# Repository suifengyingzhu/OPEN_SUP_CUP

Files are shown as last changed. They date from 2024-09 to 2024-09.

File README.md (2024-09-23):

# RM2024桂电数控超级电容方案开源

设计者：杨宇翔

文档撰写：杨宇翔 钟启源 刘宇轩

桂林电子科技大学Evolution战队

## 前言

在RoboMaster机甲大师赛事中，严苛的底盘功率限制规则迫使各参赛队伍从软件和硬件方面研究高效的功率管理方案。而我队早在2018年末便研究并开源了较具有特色的超级电容方案，但2020年，官方裁判系统超级电容管理模块与相关限制规则加入，超级电容的使用更加规范，这也给我们带来了不小的挑战。



在这个赛季，我们结合本校学长的超级电容方案，经过近一赛季的研究与测试，开发出了采用4MOS结构的两相交错Buck-Boost电路构建的超级电容方案，希望能为超电的开发研究提供一个新的思路。

## 简介

本方案中的两相交错Buck-Boost变换器是一种采用载波移相180°的控制方式的电路结构。该变换器在Buck模式和Boost模式之间切换时，能够实现能量的双向流动，并且不会产生过压与过流现象。同时，交错并联的拓扑结构可以减少电感电流的纹波，降低每相电感的体积，并提高电路的响应速度，使其极其适用于超级电容的控制中。双向BuckBoost应用已经非常普遍，对于双向BuckBoost的原理在此不再赘述。

## 拓扑介绍

### 两相交错场景

#### 优劣分析

1.低纹波。上面提及，每一相电路其实是以100Khz的频率工作的，但相比于单相输出，两相交错180度可以将电流纹波进行互补输出，理论上总输出端纹波相互抵消，电压输出波形更加平稳。由于纹波消除作用，它的有效输入与输出纹波变为 200KHz。因此在计算交错式设计的电感时，适用的频率虽和单相设计完全相同，但能允许的纹波电流却会增加一倍，使得设计所需的电感值得以减少一半，电容设计也是如此，等效后电压纹波的明显降低，使得设计所需的输出电容数量减少，节约成本的同时，也大大缩小了整个模块的体积，整个电源环路设计更加简洁。

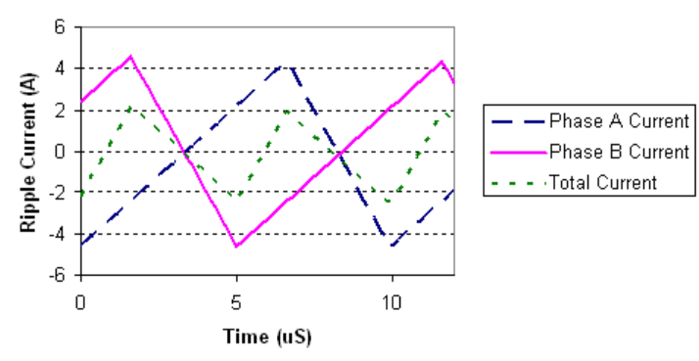
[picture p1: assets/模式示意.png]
屏幕截图 2024-07-03 203623


2.高效率。两相交错升降压电源虽然是每相将两个周期合并降频至100Khz工作，但实际总输出特性仍可等效为200Khz的工作场景。与单相相比，我们将开关管的开关频率降低，减小了开关管的开关损耗，从而进一步降低了整个电源的静态功耗，提升了整个模块的功率密度。而在负载场景下，由于每相分走一半电流，两相更好控制了电感的温度升幅，提升了模块的效率，值得一提的是，在两相交错下，电路的响应基本等同于单路电路的响应，没有受到频率降低的影响。

#### 控制方法

在低功率场景时，本方案采用两相Buck-Boost的控制方法。假设我们此时处于50%占空比时的Buck模式：在第一个周期中，第一路左边半桥的两个开关管Q1,Q2正常进行50%占空比的PWM开关，右边半桥上管Q3处于常通状态；第二路左右半桥两上管Q5,Q7处于关闭状态，两下管处于常通状态。在第二个周期中，将两路电源的开关管状态进行交换。（如图所示）

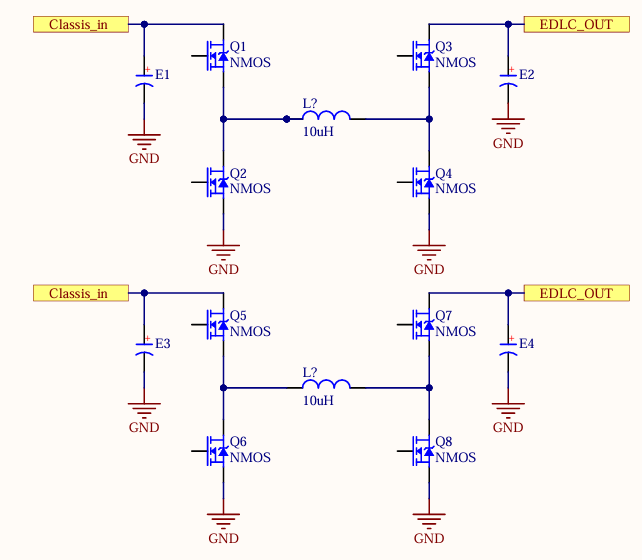
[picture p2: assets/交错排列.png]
交错排列


不难看出，两路电源每隔一个周期工作一次，并且是处于交错工作的状态。如果我们将开关频率调整至200Khz,那么此时可以把每一路电源等效为在以100Khz的频率进行开关，两相交错180度。由于我们的方案是并联两相输出，因此总输出端是互补输出的，实际整个电路的开关频率还是处于200Khz的状态。

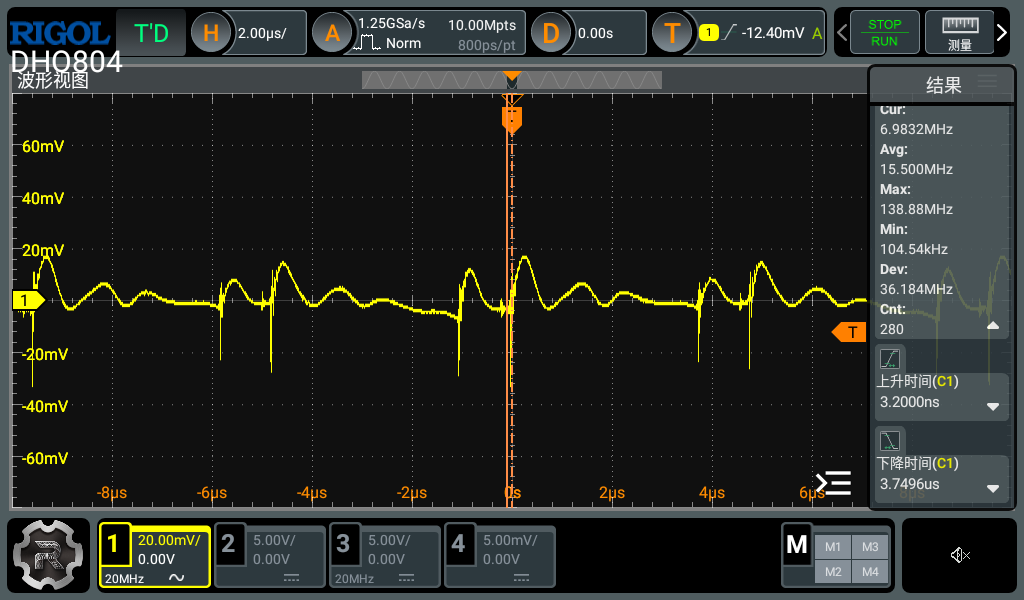
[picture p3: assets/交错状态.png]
交错状态


本超电方案的最大的劣势在于控制板上并没有太多的电容供储能使用，但电容组的存在令这一劣势的影响微乎其微，多出的空间反而使整块板的布局变得更加合理美观，功能也更加齐全，为其的使用锦上添花。

### 并联输出场景

#### 电压源并联可行性分析

 一般情况下，由于受控电压源的电压随着控制量的变化而变化，其产生的电压值不是固定不变的，根据电路理论，两个理想受控电压源中电压高的会给电压低的充电，使其电流过高，造成损坏，因此无法直接并联。

但是在实际情况下，电压源内阻以及导线电阻并非小到不能忽略。当两不同电压源同时为一个用电器供电时，根据基尔霍夫电流原理，流入等于流出，并带入数值加以计算，可以得出两电压源电压值为正数，只要保证两电压源的输出电流大于0即可保证两电压源都在向用电器输入能量。因此在实际应用中，受控电压源的并联都是采用电压源加理想二极管构成不间断电源方案，进而实现并联。然而对于双向电源来说，二极管限制了电流方向，此方案不可行。本超电方案中通过在交错状态下分时导通和并联状态下恒比例输出实现均流控制，减少环路损耗。

#### 优劣分析
对于导通损耗，损耗功率和电流的平方成正比，并联两相可以减少MOS管流过的峰值电流，减少损耗，提高效率。同时在并联状态下，电感量减半，同时带来两倍的电流斜率，此时响应也优于交错。实际控制中，采用低功率下交错，高功率和负载迁越时并联的方式，在保证最优性能的情况下最大限度降低损耗。

#### 控制方法

在高功率和负载迁越场景时，两路同步并联输出，本方案采用并联Buck-Boost的控制方法。两个并联的电压源使用。在使用时，若将右上管常导通，右下管常断开，而左上和左下管继续使用Buck电路控制策略，则完全等效于Buck电路的拓扑，此时可将电路看作同步Buck，可实现将左侧电降压后提供给右侧；若将左上常导通，左下常断开，而右上和右下继续使用Boost电路控制策略，则完全等效于Boost电路的拓扑，此时将电路看作同步Boost即可实现将左侧电升压后提供给右侧；若左右电压相近，则in半管的占空比会减少，out半管的占空比会增加，两者逐渐趋同，此时实际应用中由于最大占空比以及死区时间等限制，很难独立的使用Buck或者Boost拓扑。于是考虑用Buck控制策略控制左半桥，用Boost控制策略控制右半桥，此即为buck-boost电路。在任意时刻，电路可视为Buck电路或Boost电路。此时，无论是使用叠加原理还是通过伏秒平衡定律，我们都可以得到如下结果 Vleft/Vright=Dright/Dleft ，其中， Dleft 为左侧上管占空比， Dright 为右侧上管占空比。

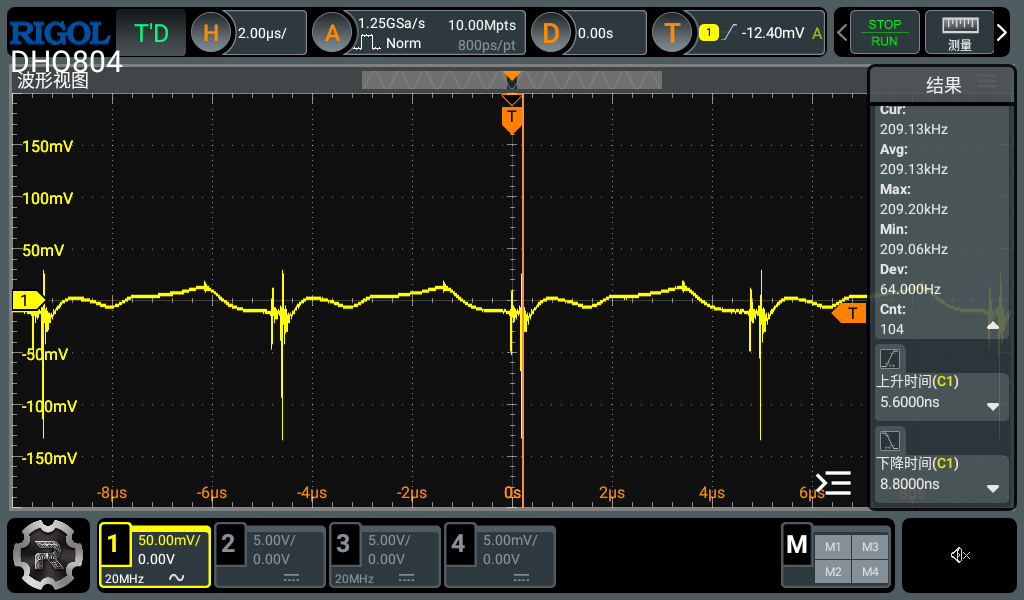
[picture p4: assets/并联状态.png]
并联状态


## 效率提升

在高负载下，超电控制模块的温度会会显著提升。一般的应对方法是利用一些降温手段，如采用铝基板、添加散热片、甚至是加装散热风扇来保证持续高负载下模块的性能。而我们更倾向于从源头解决问题——提高模块的效率，即通过一些硬件设计和软件控制的方式，降低电能转化成的热能，从而减少电能的流失，最终达成提高效率的目的。这从一方面来看，能高效地将底盘电能搬运储存，或是将超电中储存的电能最大程度输送回底盘供电，提升机器人的性能；另一方面，减少模块的发热，也就能控制模块的故障发生率，保证机器人在运行中用电的稳定性和安全性。

那么，如何提高模块的效率？首先我们要考虑的是实际使用过程中哪里会让其产生损耗，这样才能对症下药。例如，电流在回路传输过程中，导线和采样电阻都会发热；四开关管频繁的开关过程中也会产生不小的损耗；电感、电容参数计算不准确会产生更多的损耗······

接着，我们就要考虑如何尽最大可能地减少这些损耗。从分析模块的电流环路，优化PCB布局，减小电流环流面积等方面下手是个不错的选择，当然，器件的摆放也很关键，良好的布局才能保证超电拥有优异性能的同时又能有良好的散热性。下图为持续负载30A 1小时下的温度图像，分散的两个环路使得散热效率大幅提升，同时优化的电流环路在最小环路面积下使得电路损耗降低。

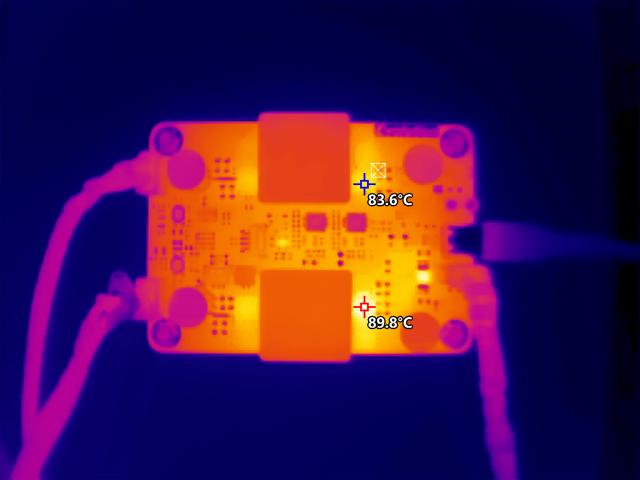
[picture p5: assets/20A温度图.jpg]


效率提升最重要在于考虑元器件所造成的损耗。在实际使用过程中，电感和开关管的发热是比较明显的，故从这二者下手。改善电感效率的重心在于参数的计算和电感的选型，我们采用的是饱和电流30A的一体成型电感，在实际测试中，两路共30A时电感温度稳定在60摄氏度左右。MOS管的损耗主要为开关损耗和导通损耗：导通损耗是MOS管在工作状态时Rds(on)产生的，公式为

P=Io²×Rds(on)

而开关损耗的产生则是因为MOS管虽然是电源型器件，但是由于极间结电容的存在，MOS管漏源极导通需要栅极驱动电流充电后才能正常打开，关闭时亦是如此，公式为

P=Qg×Vg×fsw×2

开关管所产生的损耗可以通过硬件选型和软件控制这两种方式来降低。首先是MOS管的选型，从公式不难看出产生的损耗主要是由Rds(on)和Qg这两个参数决定的，在选型时应仔细斟酌其内部材料的使用，比较得出性能更加突出的选型。当然，由于栅极上升沿时间的存在，MOS管若不能及时打开或关闭，也会造成更多的损耗，且如果续流管没有及时打开，只能通过自身的体二极管续流，此时产生的损耗是极其严重的。解决该问题的办法一般是更换Qg更小的MOS管或者增加驱动电流，我们选用的栅极驱动是LM5109，该芯片能提供持续1A的驱动电流，实测使用此芯片模块上MOS管栅极上升沿约为50纳秒，同比其他芯片更为迅速。同时，我们采用自举的方式为半桥供电，因此由于自举电容充电时间和栅极驱动时间的限制，模块不能到达100%占空比。软件降低损耗主要采用上面介绍的交错两相控制的方法，这样不仅能让两路均流，使得单路导通损耗减少，MOS管发热减小，而且将200Khz的开关频率降低一半，也能使开关损耗降低，并且将模块输出的最高占空比提高至100%。

## 多拓扑结构 

模块预留了两个大电流跳线点，通过改变跳线点的连接状态，可将结构改为双通道独立输入输出，单通道交流输出，升降压稳压型UPS（输出稳压型超电，如30v供电轮系）如下图所示，为备赛电赛提供更多选择。对于这些拓扑结构都已进行验证，这部分的代码之后将示完成度开源。
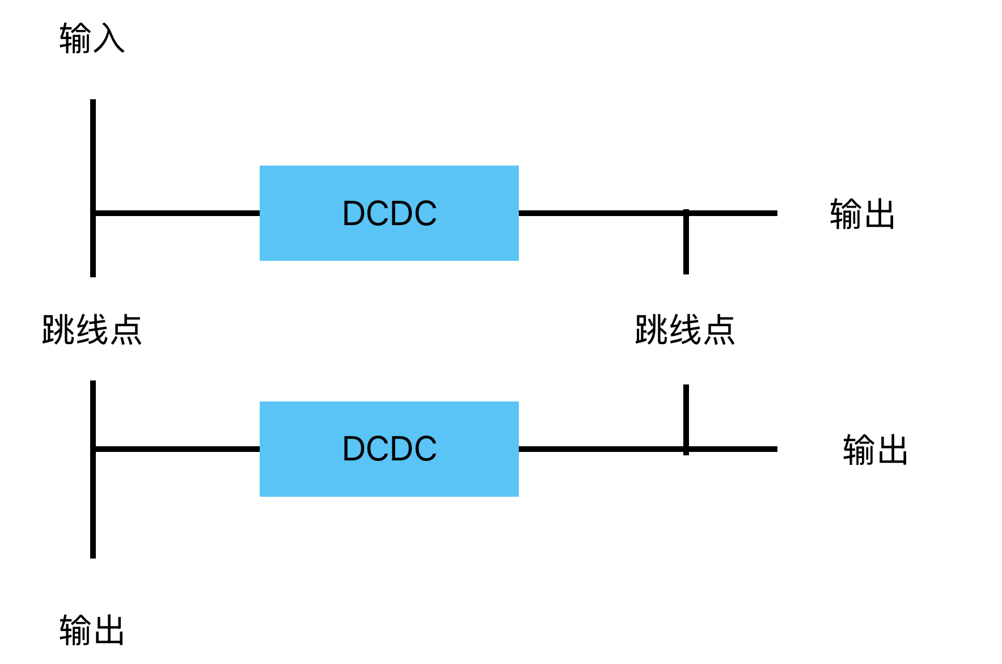
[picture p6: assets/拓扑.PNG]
拓扑


## 输入输出参数

### 额定最大值

输入电压8-30V，电容端单通道瞬态30A，持续负载10A。双通道瞬态60A（电容组60A恒流输出持续到没电），持续负载20A.（无散热片和风冷）

电容端输出2-30V，底盘输出端12-30V（单通道升压版可到40V）

### 输出波纹值

可以对输入，输出，电容组处电压进行测量，监测控制模块的实际输出电压。

确保输出电压在设定范围800mV内，静态波纹70mv, 10W-400W迁越负载电压波动1200mV，1A-20A ,2500mA/us负载斜率下恢复时间1ms。具备多端电流测量，监测功率控制模块的实际输出电流。确认输出电流与设定值相符，辅助功率控制，并在需要时进行调整。

## 保护机制

超电烧毁乃兵家常事，为保证超电正常稳定运行，项目成立之初就提出要完善其自身的保护机制，延长其使用寿命。（超电控制板成本在200元左右，也是为了减少此项支出）

硬件件具备输入输出TVS、输入欠压保护机制。

软件具备过载、电容组过压、输入欠压、电容组欠压、模组元器件损坏的保护机制，并可在模块无永久性损坏风险的情况下自行恢复。

确认保护触发后，系统能够在1ms内停机或采取其他适当的措施。

触发自锁保护后，仅能在模块状态正常后通过断电重启解除保护，系统严重损坏后保护可能失效。

自锁保护状态：输入欠压保护，电容端过压保护，输出端过压保护（刹车时产生过高电动势，超级电容无法完全吸收），过流保护，MOS损坏保护

得益于交错模式的超快响应和极强的过流能力，虽然设有如上保护，但其从未在赛场上触发，从联盟赛上场至今，超电在赛场上保持着0失误的记录。

## 上位机

为方便功能的维护和升级，还配套制作了上位机程序。由于控制逻辑过于复杂，为保证逐周期环路计算，代码不得不做许多优化，包括但不限于大量内敛，导致代码逻辑十分混乱，且没有注释，代码部分待优化完成后开源，如需尝鲜的兄弟可以通过上位机下载代码。

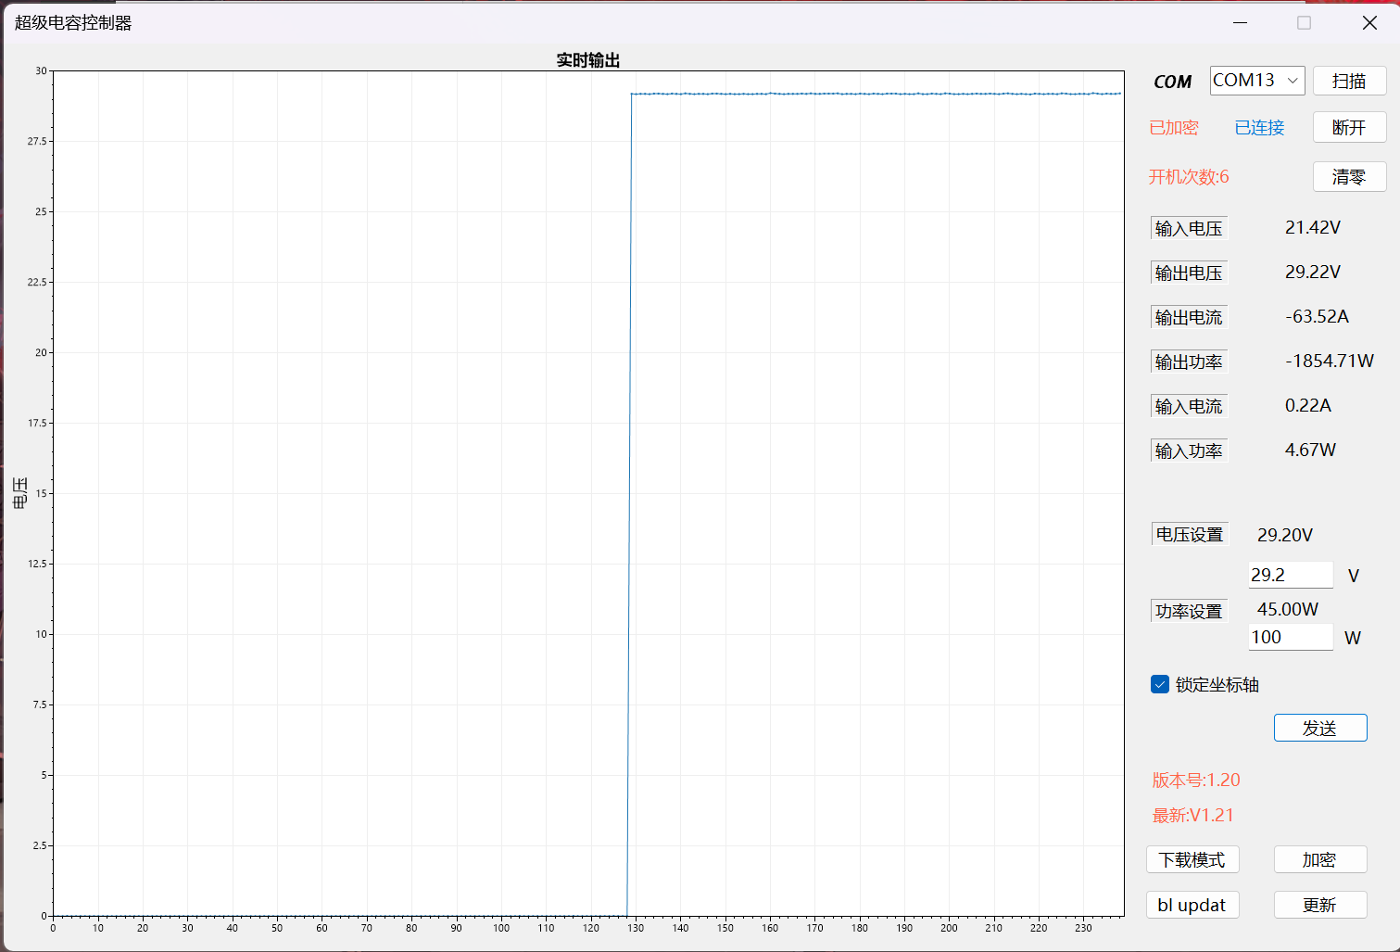
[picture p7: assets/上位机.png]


因代码中没有使用输出电流检测，故大部分板子没有焊电流感应放大器，该功能正常可用。

## 结语

祝愿大家超电永远不烧！！！

联系方式
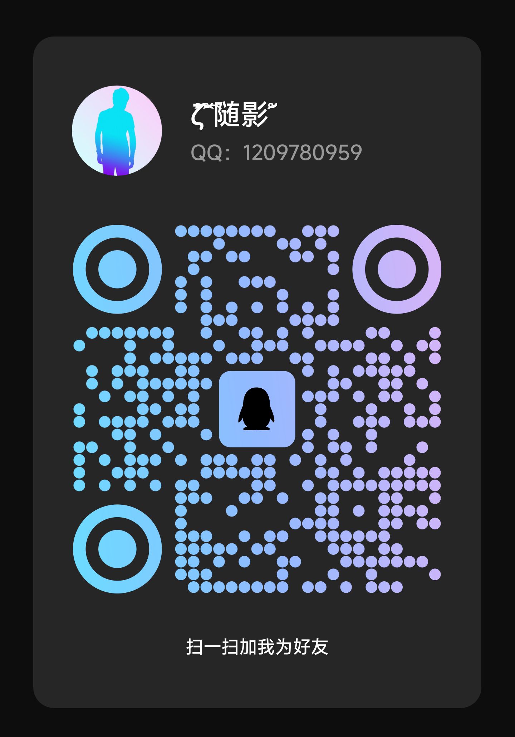
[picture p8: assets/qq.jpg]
qq


# 测试报告

## Output Ripple

### 测试图

4A负载下输出纹波

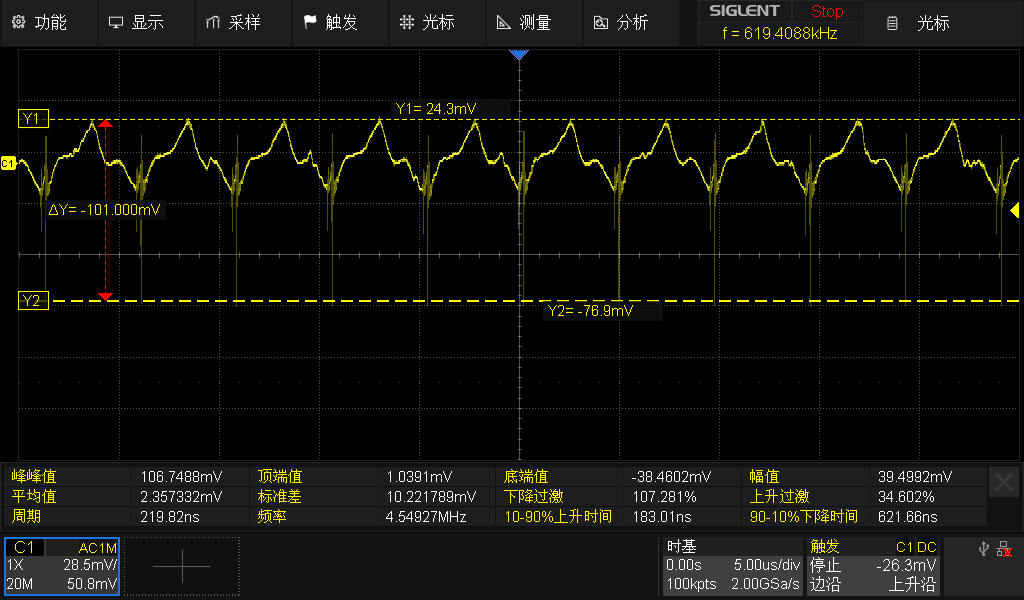
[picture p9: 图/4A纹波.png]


8A负载下输出纹波

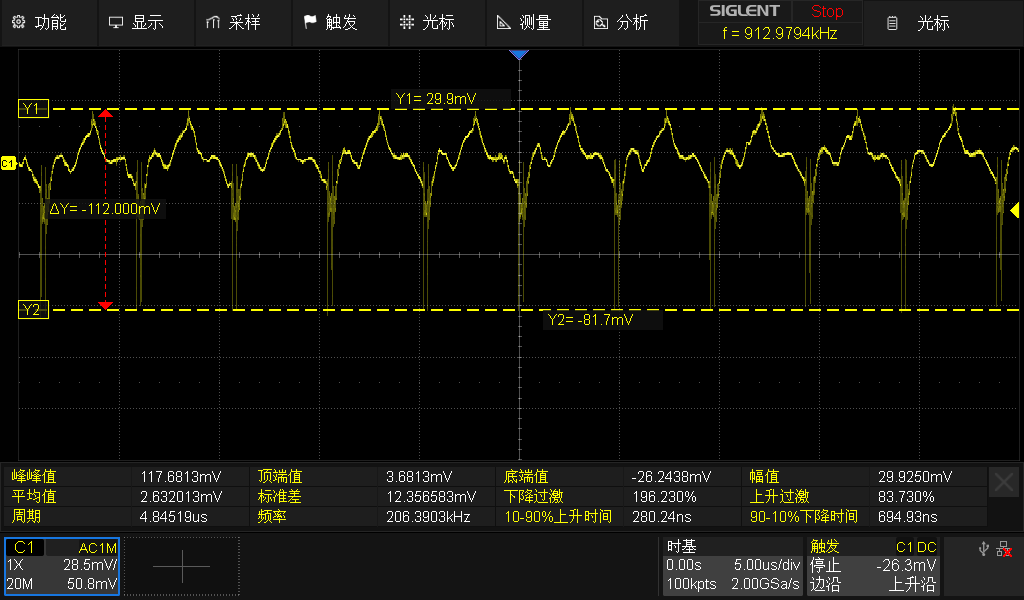
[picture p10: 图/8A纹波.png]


12A负载下输出纹波

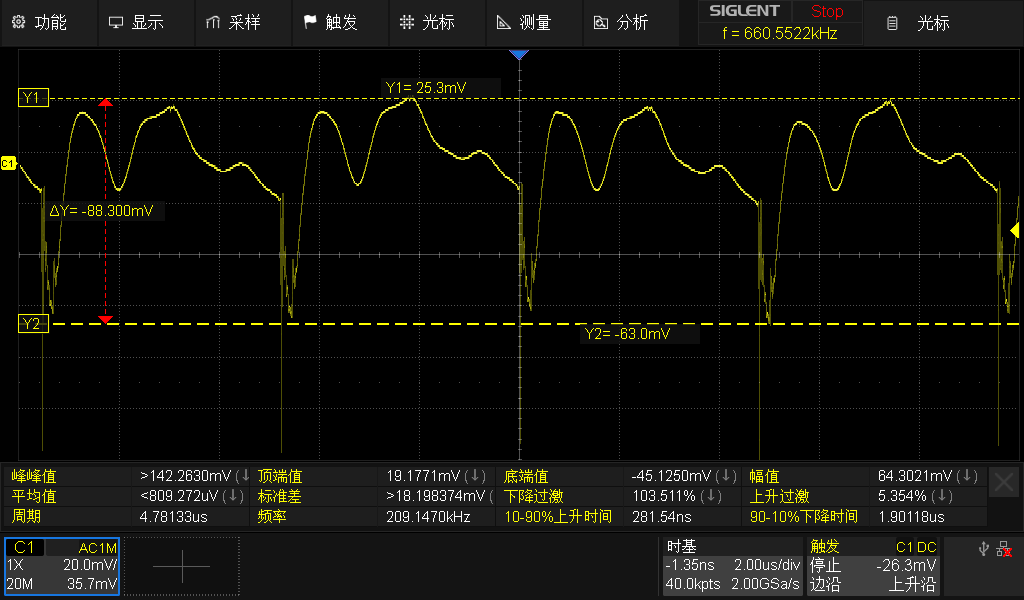
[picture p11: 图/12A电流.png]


16A负载下输出纹波

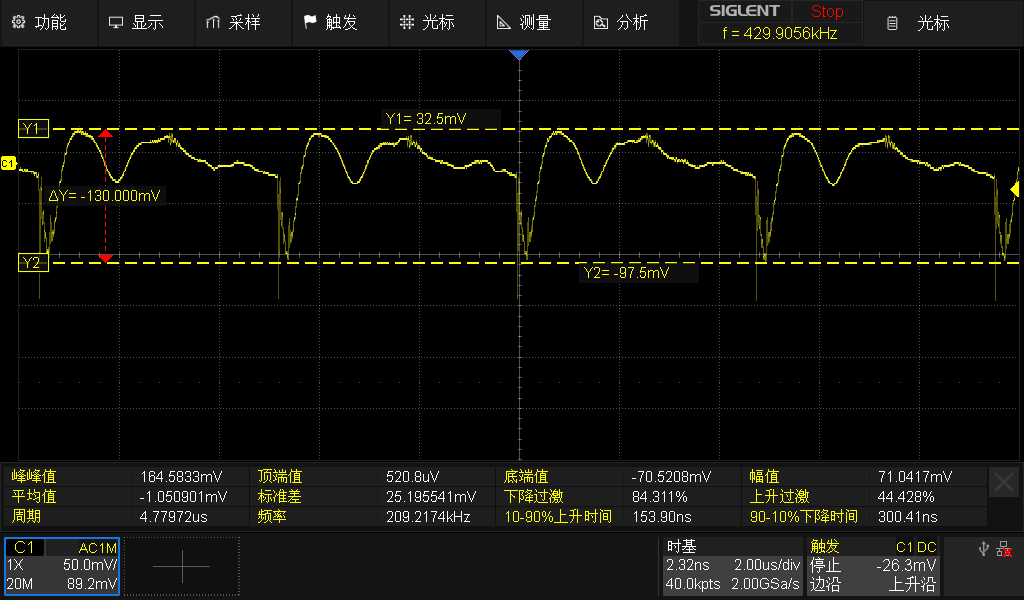
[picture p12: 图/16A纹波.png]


20A负载下输出纹波

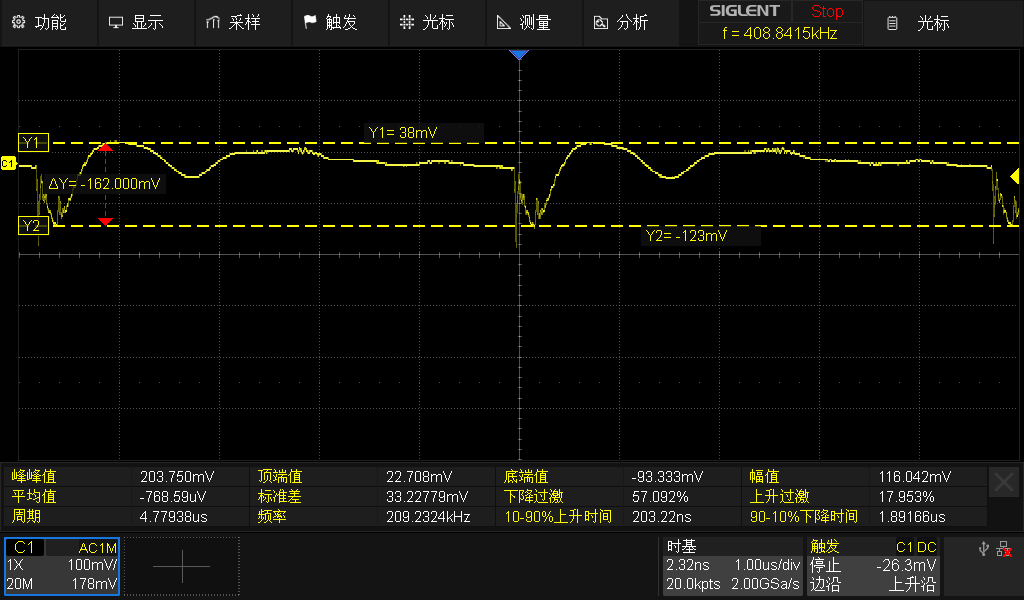
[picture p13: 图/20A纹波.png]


### 测试分析

注：以下测试分析将引用KEYSIGHT旗下的电源E36150的电源参数进行比较分析。

根据波形可以看出，随着负载增大，输出端纹波有明显增加。这是由于模块设计时受PCB尺寸限制，输出电容未使用更大容值的固态电容，导致模块在工作过程中输出端电容充放电电荷量改变，引起电容电压波动量增加，进而提高了输出的纹波率。在输出电流16A负载下，模块的输出纹波为71mV，在额定输出电流20A负载下，模块的输出纹波为162mV，计算可得纹波率为1.08%，在RM的应用场景中，此纹波率已满足系统的正常运行。在额定电压、电流输出下，E36150最大输出纹波小于75mV，在与产品级的电源输出纹波比较下，此模块还是存在较大的差距。

## Transient

### 测试图

Ilow=1A Ihigh=12A Slew rate=2.5A/us F=100Hz

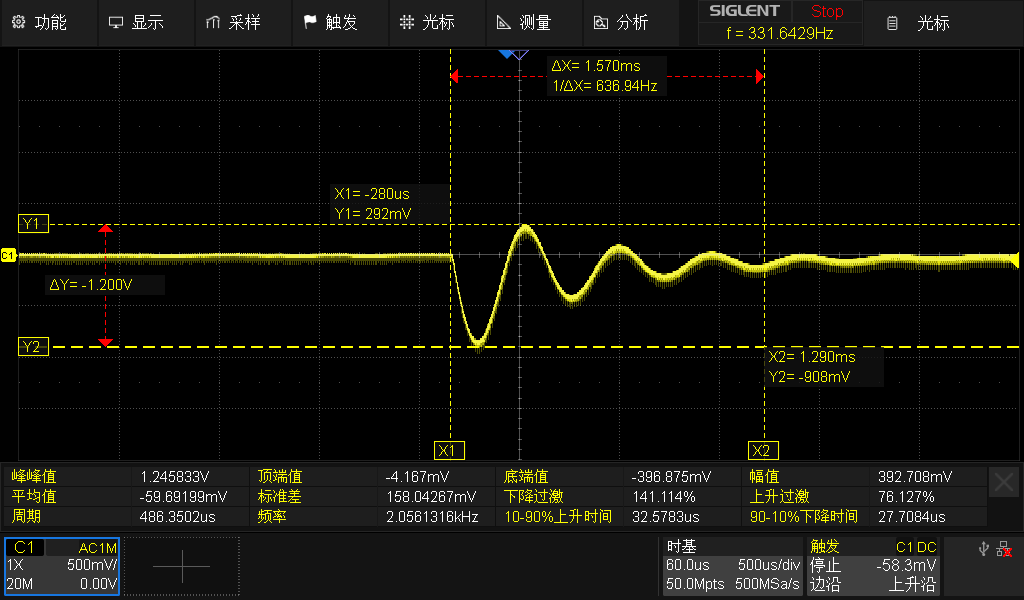
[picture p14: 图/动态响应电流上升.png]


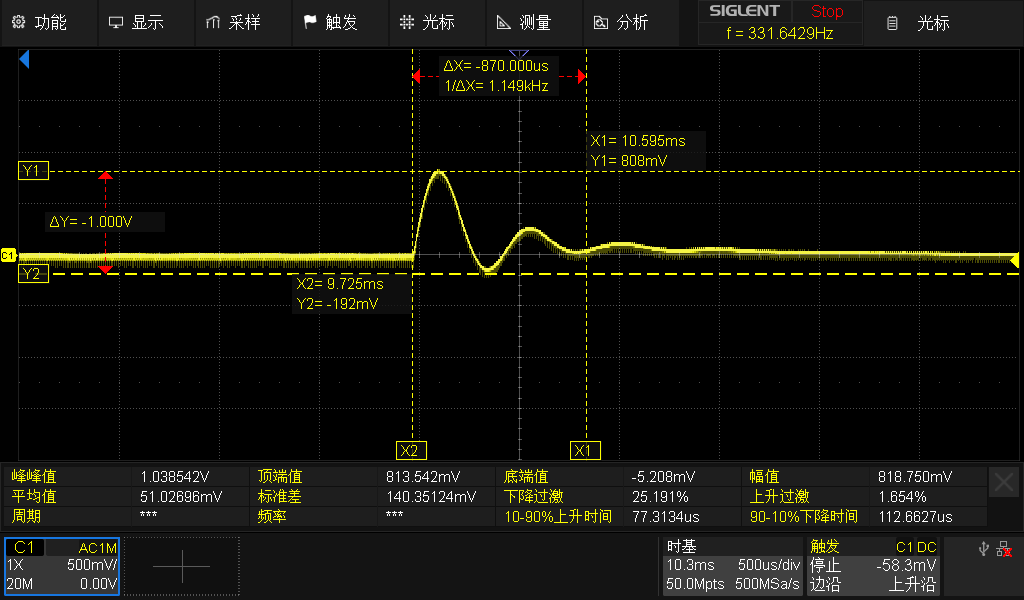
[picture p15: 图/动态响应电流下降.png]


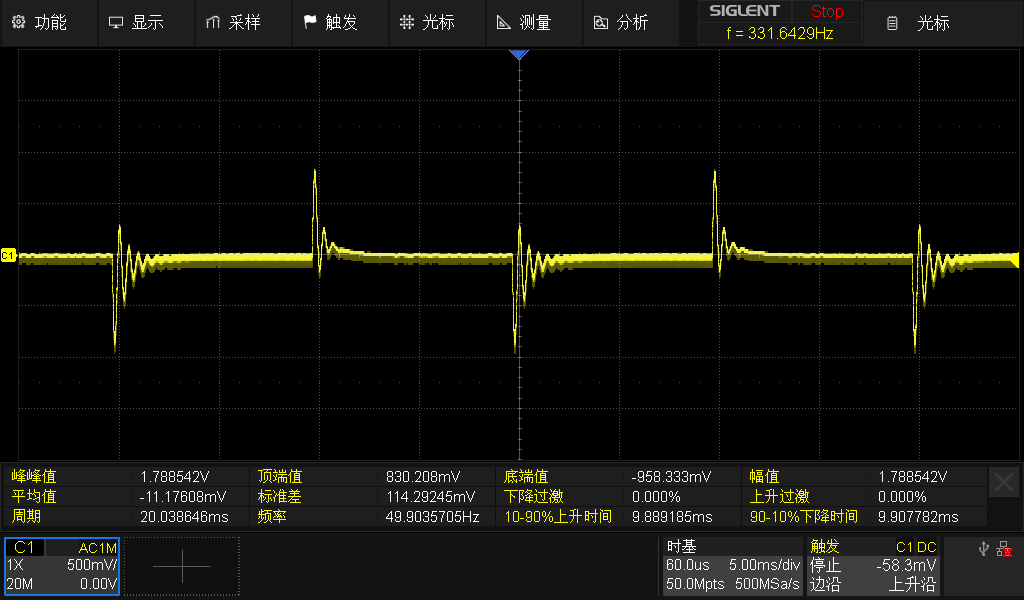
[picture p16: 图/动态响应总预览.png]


负载拉低：振铃峰峰值1V，恢复时间0.8ms；负载拉高：振铃峰峰值1.2V,恢复时间1.6ms。

测试结果可知，模块在负载拉低状态下的动态响应明显优于负载拉高状态下的动态响应。负载拉高时，产生振铃的峰峰值高，会出现一小段过冲反馈欠阻尼现象，且恢复时间较长，系统发生震荡后收敛周期更长。负载拉低时，恢复时间相较短，且无明显过冲现象，在产生振铃后波形迅速收敛。E36150电源的动态响应不超过1ms，这点与我们模块较为相近，但是E36150的Voltage Settling Band为150mV，且反馈阻尼效果好，不会发生过冲现象，并且系统不会发生持续震荡，这点我们模块是比较欠佳的。作者在测试时，在仅运行环路计算，且优化参数后，1-10A动态响应测试下，环路响应在100us左右，且电压波动小于静态波纹70mv。双通道的环路控制逐周期计算，要求算力过大，目前使用PI双环，未能使用最高电流斜率，最终未能达到该最优响应，后续会优化此环路计算以获得更高动态响应。

## Load Regulation

### 测试图

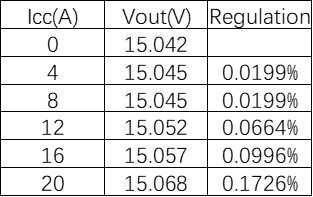
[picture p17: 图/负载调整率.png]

### 测试分析

测试结果可知模块在不同的稳定负载下，输出电压示数趋于稳定，无明显波动，且输出电压处于设定5%区间内，满足正常工作要求。E36150电源的负载调整率为0.01%±2mV，我们模块在额定电流60%以下时负载调整率可达到此参数，但是超过该区间后，负载调整率表现稍逊。

## MOS Vds Spike

### 测试图

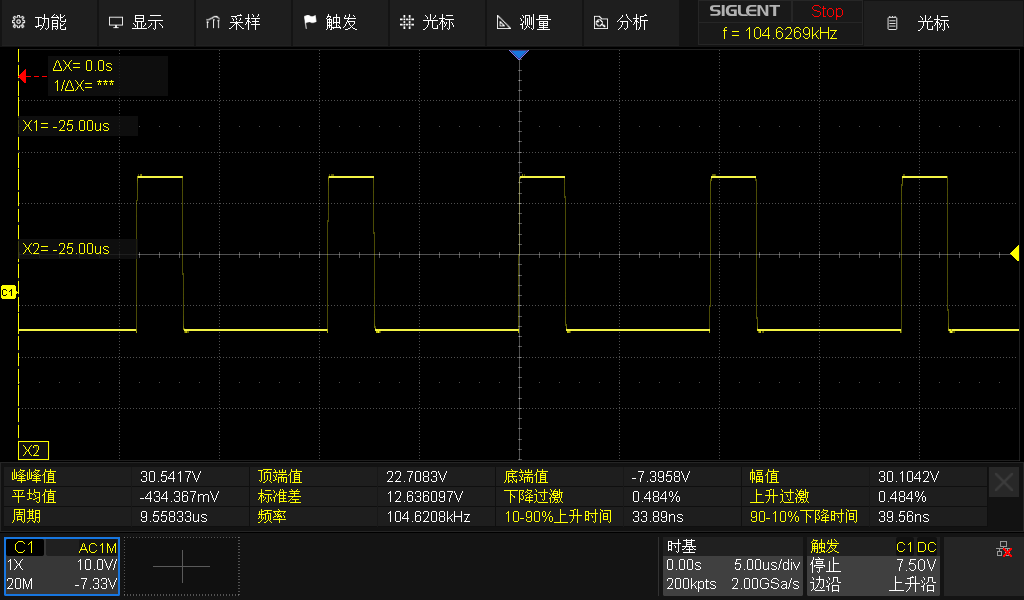
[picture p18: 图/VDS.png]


### 测试分析

测试了模块频繁开关的MOS管Vds波形，均如上述测试图所示，开关时无过冲现象。且波形稳定，无二次开启、误关断等不良现象。

## Efficiency

### 测试图

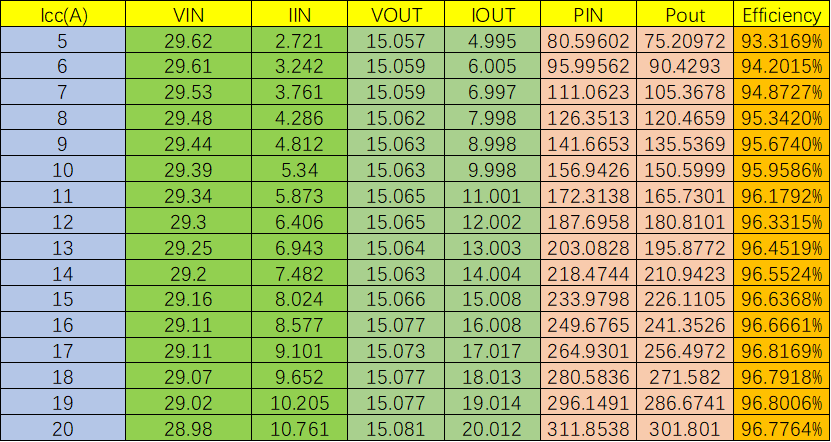
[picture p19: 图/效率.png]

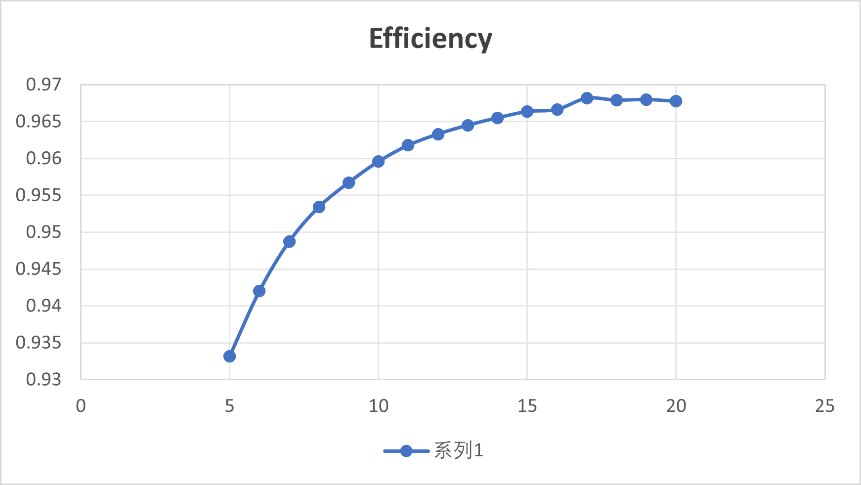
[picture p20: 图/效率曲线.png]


### 测试分析

模块的静态功耗约为2.7W，在低负载下，模块效率达到93%，而在负载施加至额定电流的60%以上后，效率稳定达到96.5%以上。参考车载标准80plus能效标准，10%负载90%效率，20%负载92%效率，50%负载94%效率，100%负载90%效率。在此标准下，我们模块在额定功率的每个负载段效率都表现良好。

### Rise Time & OverShoot

### 测试图

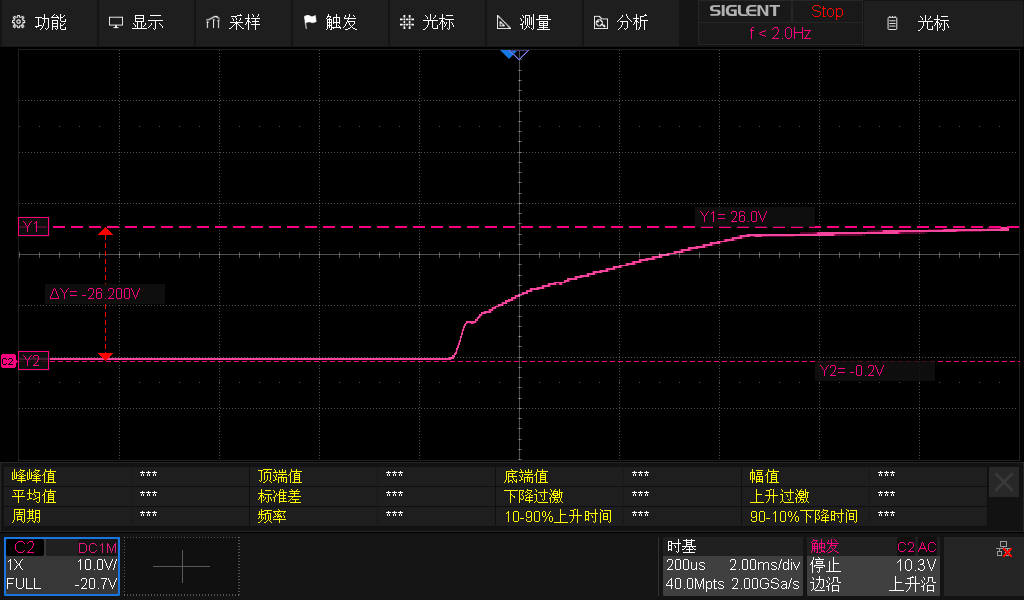
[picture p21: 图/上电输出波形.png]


### 测试分析

模块上电输出端波形正常，无过冲现象。且做到输出端启动软开关，保护后级负载不受启动时电压应力和冲击电流影响。电压上升时间约3ms，既满足缓启动要求，也不会因为上升时间过长影响后级电路的正常启动工作。

## Line Regulation

### 测试图

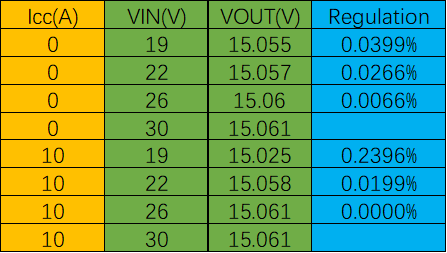
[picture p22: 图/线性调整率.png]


### 测试分析

测试结果表明，模块在空载和负载10A的测试环境下，输入电压发生改变时，输出电压恒定值均处于设定输出电压的5%区间之中，模块线性调整率正常。E36150电源的线性调整率为0.01%±2mV，我们模块在与最大输入电压压差10V以上的时候，线性调整率数据达不到此标准。

未经许可禁止商用！！！

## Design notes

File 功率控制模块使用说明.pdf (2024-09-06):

# 功率控制模块使用说明

功率控制模块用于控制底盘电路的功率的模块。可以用于各种应用，例如调整电压、电 流或频率，以实现对设备的精确控制，下文使用“模块“作为功率控制模块的简称。
⚫ 输入输出参数监控：
1. 额定最大值：
| 输入电压 8-30V，电容端单通道瞬态 30A，持续负载 10A。双通道瞬态 60A，持续负载 20A.
| 电容端输出 2-30V，底盘输出端 12-30V（单通道升压版可到 40V）
2. 实际输出电压，电流：

可以对输入，输出，电容组处电压进行测量，监测控制模块的实际输出电压。

确保输出电压在设定范围 800mV 内，静态波纹 70mv, 10W-400W 迁越负载电压波动 400mV，1A-

12A ,2500mA/us 负载斜率下恢复时间 1ms。具备多端电流测量，监测功率控制模块的实际输出电流。确认

输出电流与设定值相符，辅助功率控制，并在需要时进行调整。

3. 效率和功率因数：

监测功率控制模块的效率和功率因数，以确保系统在最佳效能下运行。

可通过调整控制模块的参数，优化效率和功率因数。
⚫ 保护触发监控：

软件具备过载、电容组过压、输入欠压、电容组欠压、模组元器件损坏的保护机制，并可在模块无永

久性损坏风险的情况下自行恢复。

确认保护触发后，系统能够在 1ms 内停机或采取其他适当的措施。自锁保护触发后，在未确认错误类

型前请不要尝试断电重启。

触发自锁保护后，仅能在模块状态正常后通过断电重启解除保护，系统严重损坏后保护可能失效。

自锁保护状态灯呈红灯闪烁状态：

1. 红灯长闪：MCU 状态异常保护（进入调试模式，下载代码）。
2. 红灯闪烁 ID：（间隔 2000ms，闪烁 n 次）
| 1：底盘功率超出电容组缓存能力，在裁判系统判罚前断电（没电了）。
| 2：输入欠压保护。
| 3：暂未使用。
| 4：电容端过压保护，输出端过压保护（刹车时产生过高电动势，超级电容无法完全吸收）。
| 5：过流保护，模组元器件损坏等严重错误
⚫ | 数据记录和报告：

数据记录功能记录输出参数的历史数据。（需连接上位机）

远程监控（需连接上位机及无线串口模块）：

支持远程监控功能，可远程监控系统运行状态。
⚫ 反馈系统校准：

功率控制模块配备了反馈系统，使用前建议校准确保反馈系统正常运行。

建议根据需要对反馈系统进行校准，以提高系统的稳定性和精度。
⚫ 保护功能：

模块具有硬件过压、欠压、输入反接等保护功能。

建议根据实际情况设置软件保护阈值参数，以确保设备在异常情况下能够及时停机或采取适当的保护

措施。

⚫ 安装和连接：
在使用之前，确保正确安装功率控制模块，并根据裁判系统说明正确连接所有电源和信
号 | 线 | 。

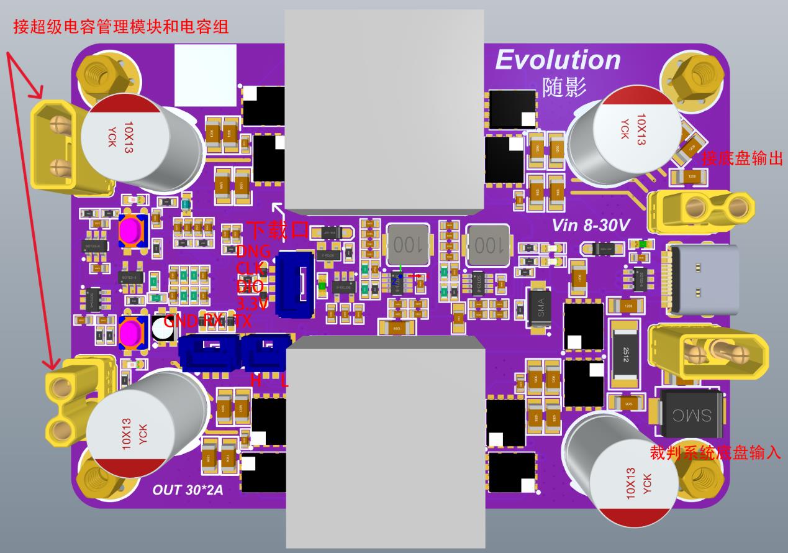
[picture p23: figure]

旧版本 CAN 信号线是反的（24.1.12）。
⚫ 通信协议：
可使用 USB_CDC，USART，CAN 控制
控制格式
字节 | ID | 1 | 2 | 3 | 4 | 5 | 6 | 7 | 8
类型 | 0x010 | ‘\’ | uint8_t | uint8_t | uint8_t | uint16_t | | uint16_t
说明 | 仅 CAN | 包头 | 电容满 电电压 (V) | 底盘功 率限制 (W) | 底盘缓 存功率 (J) | 底盘功率(W，放大 100 倍，既 1222 为 12.22W) | | CRC16

回报格式

字节 | ID | 1 | 2 | 3 | 4 | 5 | 6 | 7 | 8
类型 | 0x011 | ‘\’ | uint8_t | uint8_t | uint8_t | uint8_t | uint8_t | uint16_t
说明 | 仅 CAN | 包头 | 底盘输 出功率 (W) | 底盘输 入功率 (W) | 底盘功 率限制 (W) | 电容电 量（单 位%） | 超级电 容状态 | CRC16

UART 使用空闲中断接收，请不要连续发送，保持至少 20ms 间隔，以保证通讯正常。

⚫ LED 状态指示
1. 正常上电呈呼吸彩灯
2. 异常上电呈红色呼吸
3. 接收到设置指令后为单色呼吸灯，指示电容电量（>90%绿灯，>60%紫灯，>30%
| 黄灯，<30%红灯）
4. 连接上位机时为蓝色呼吸灯。
5. 错误时为红灯快闪

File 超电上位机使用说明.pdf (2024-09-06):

# 超电上位机使用说明

当超电控制模块接入上位机后，可以对其进行固件更新，状态检测，加密擦除等操作。

在连接上位机时

下载代码


下载固件时，请断开电源和电容组，使用 USB 连接上位机，否者模块可能烧毁。

全新的超电控制模块下载代码时，需要手动进入 Bootloader，按住 BOOT 按键，在短按复位键，即

可硬件进入 Bootloader，此时点击 bl update 刷入 Bootloader 固件，下载成功后复位，超电控制模块将

进入下载模式，此时点击更新刷入 APP 固件，如果已经刷入 Bootloader 固件，此时系统回自动跳转 APP

固件并连接上位机，但此时模块未加密，无法正常使用，点击加密可对模块进行加密，此后更新固件将不

会影响加密状态，如无法加密，请尝试重新连接。

此后更新只需点击更新即可。

灯效补充说明

⚫ 上位机模式：

当打开上位机，插入 USB 时，自动进入上位机模式，此时状态灯呈淡蓝色呼吸灯。

⚫ 下载模式：

软件使用 AB 分区存放固件，一个分区存放 Bootloader，另一分区存放 APP 固件。

进入下载模式后状态灯亮紫色呼吸灯，如 2 秒内未连接 USB HOST（既电脑）将会尝试切换到另一分

区。

下载模式状态灯呈呼吸状态：

1. 红灯：擦除扇区。
2. 蓝灯：下载固件。

⚫ 保护触发监控：

软件具备过载、电容组过压、输入欠压、电容组欠压、模组元器件损坏的保护机制，并可在模块无永

久性损坏风险的情况下自行恢复。

确认保护触发后，系统能够在 1ms 内停机或采取其他适当的措施。自锁保护触发后，在未确认错误类

型前请不要尝试断电重启。

触发自锁保护后，仅能在模块状态正常后通过断电重启解除保护，系统严重损坏后保护可能失效。

自锁保护状态灯呈红灯闪烁状态：

3. 红灯长闪：MCU 状态异常保护（进入调试模式，下载代码）。
4. 红灯闪烁 ID：（间隔 2000ms，闪烁 n 次）
| 1：底盘功率超出电容组缓存能力，在裁判系统判罚前断电（没电了）。 2：输入欠压保护。 3：暂未使用。 4：电容端过压保护，输出端过压保护（刹车时产生过高电动势，超级电容无法完全吸收）。 5：过流保护，模组元器件损坏等严重错误

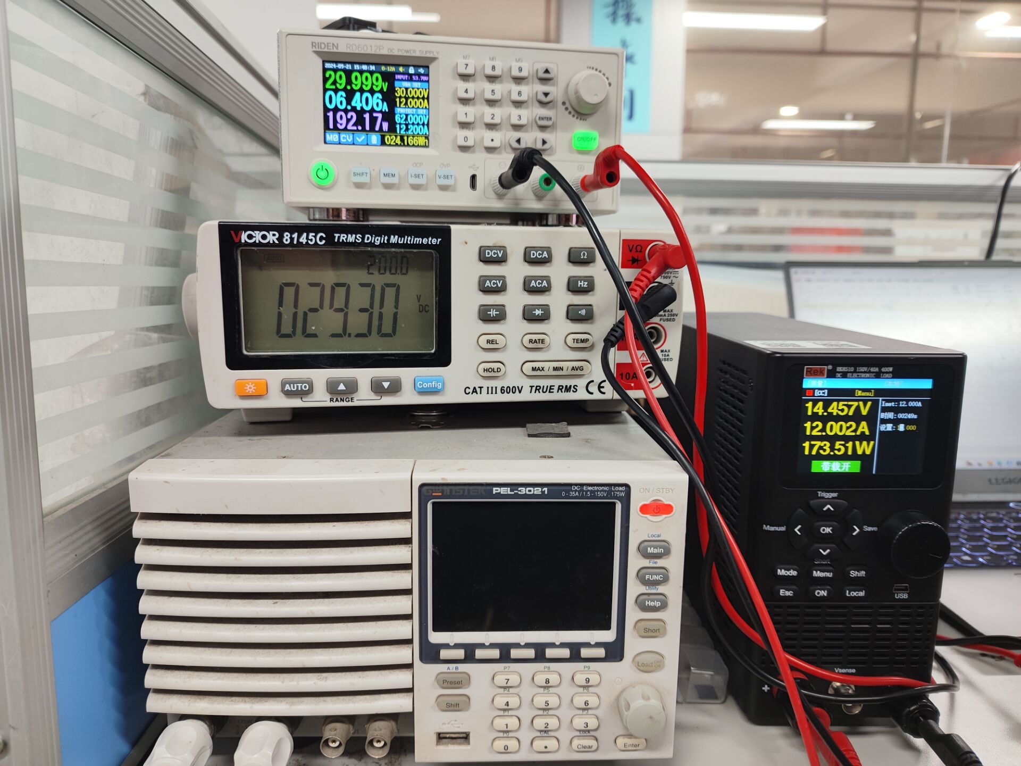
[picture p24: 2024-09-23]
图/12A输入端.jpg

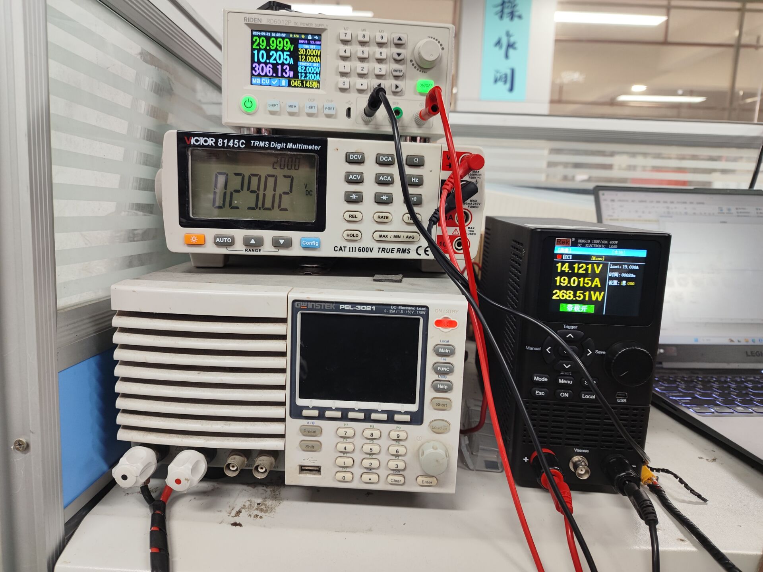
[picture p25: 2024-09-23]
图/19A输入端.jpg

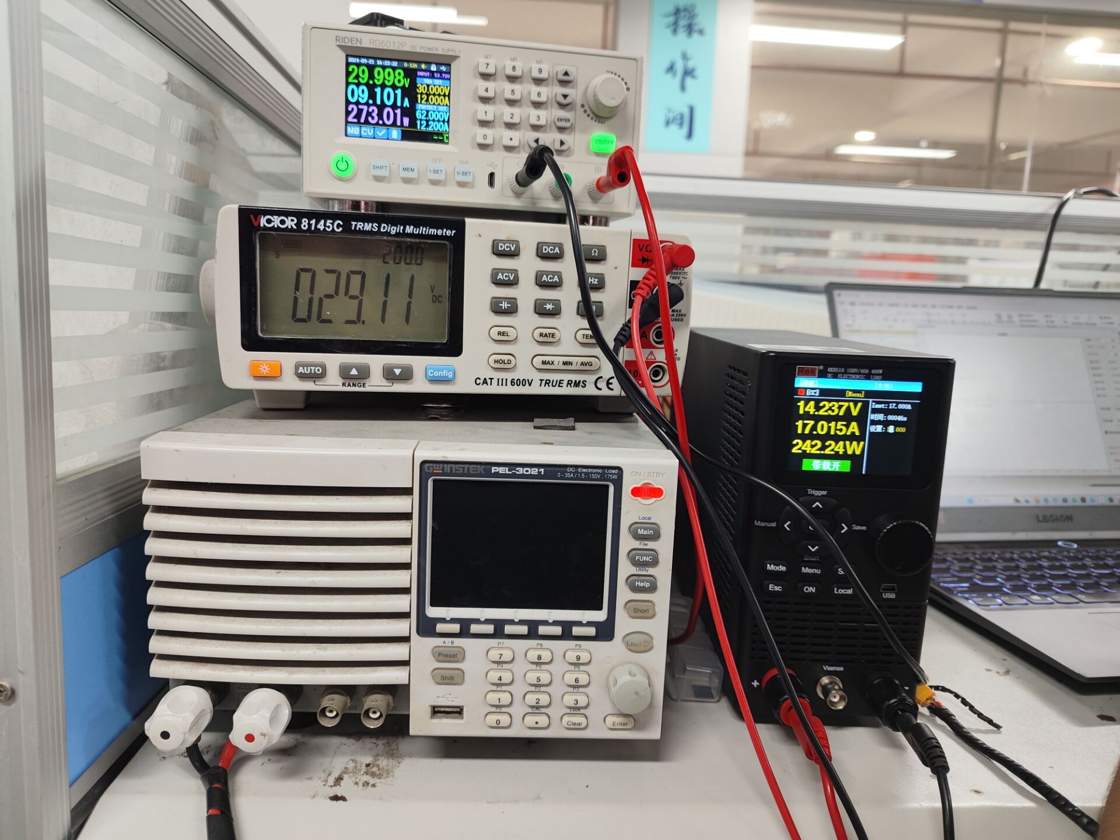
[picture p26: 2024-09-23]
图/17A输入端.jpg

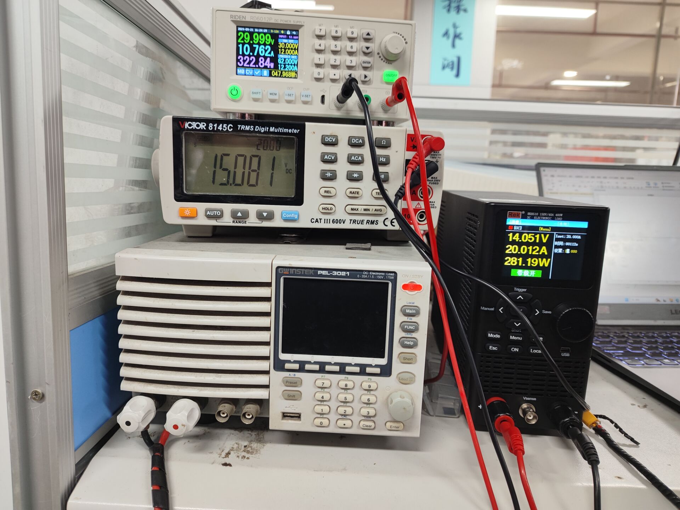
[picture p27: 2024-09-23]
图/20A输出端.jpg

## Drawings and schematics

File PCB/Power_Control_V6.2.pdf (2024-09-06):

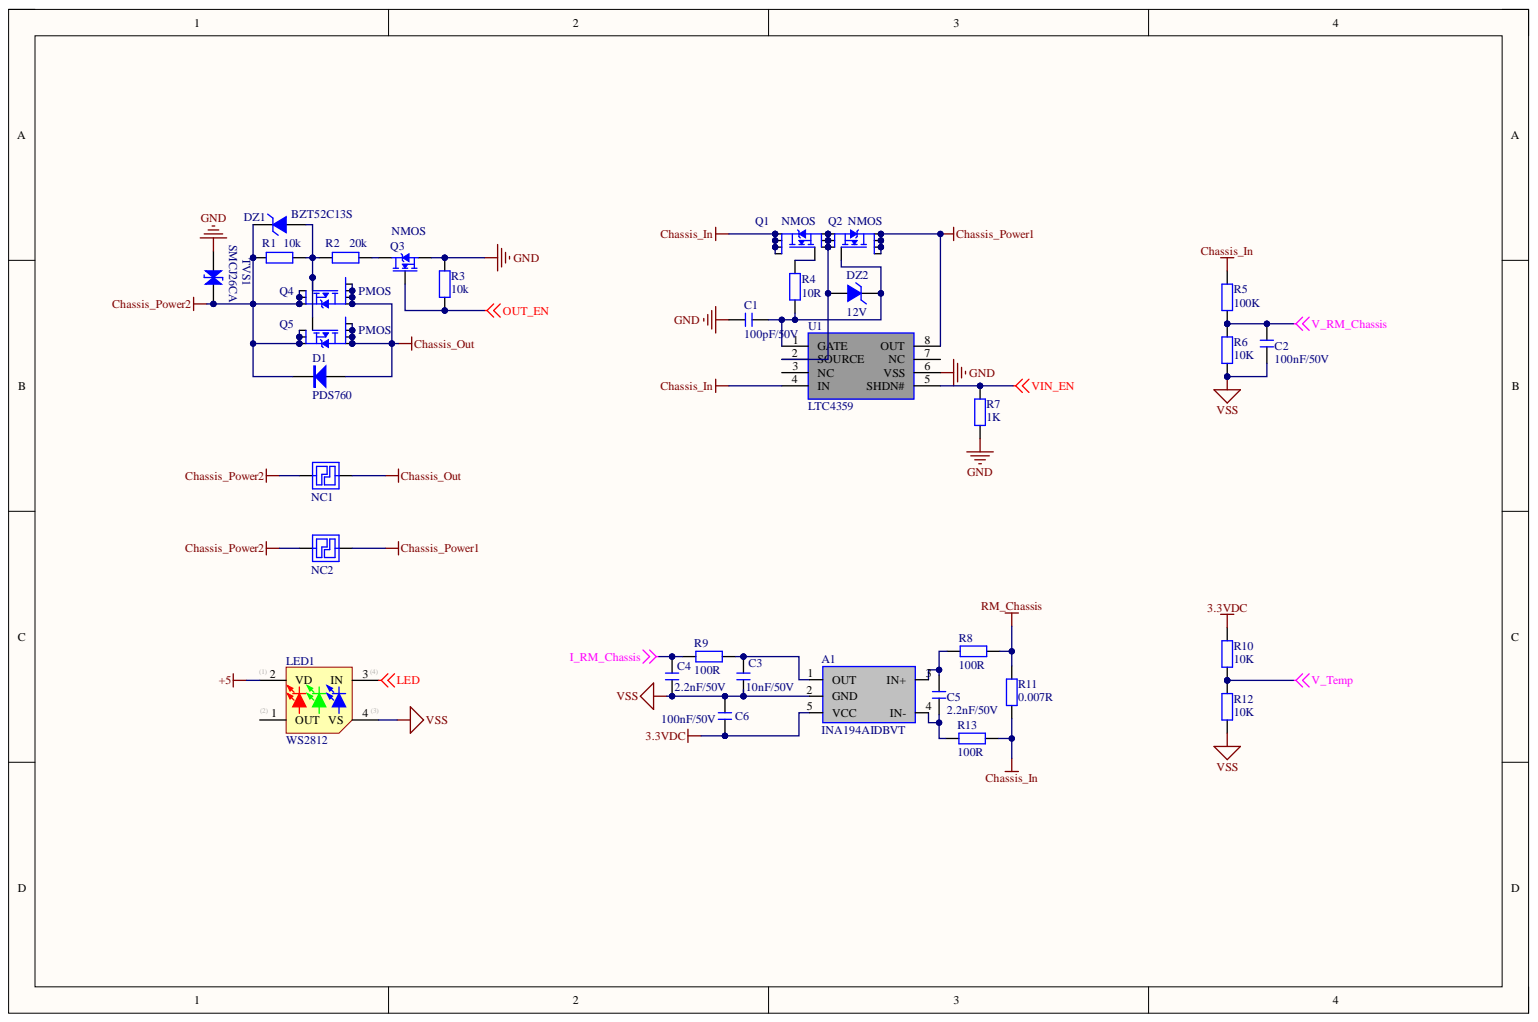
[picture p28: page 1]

G SO | C VSS D N#

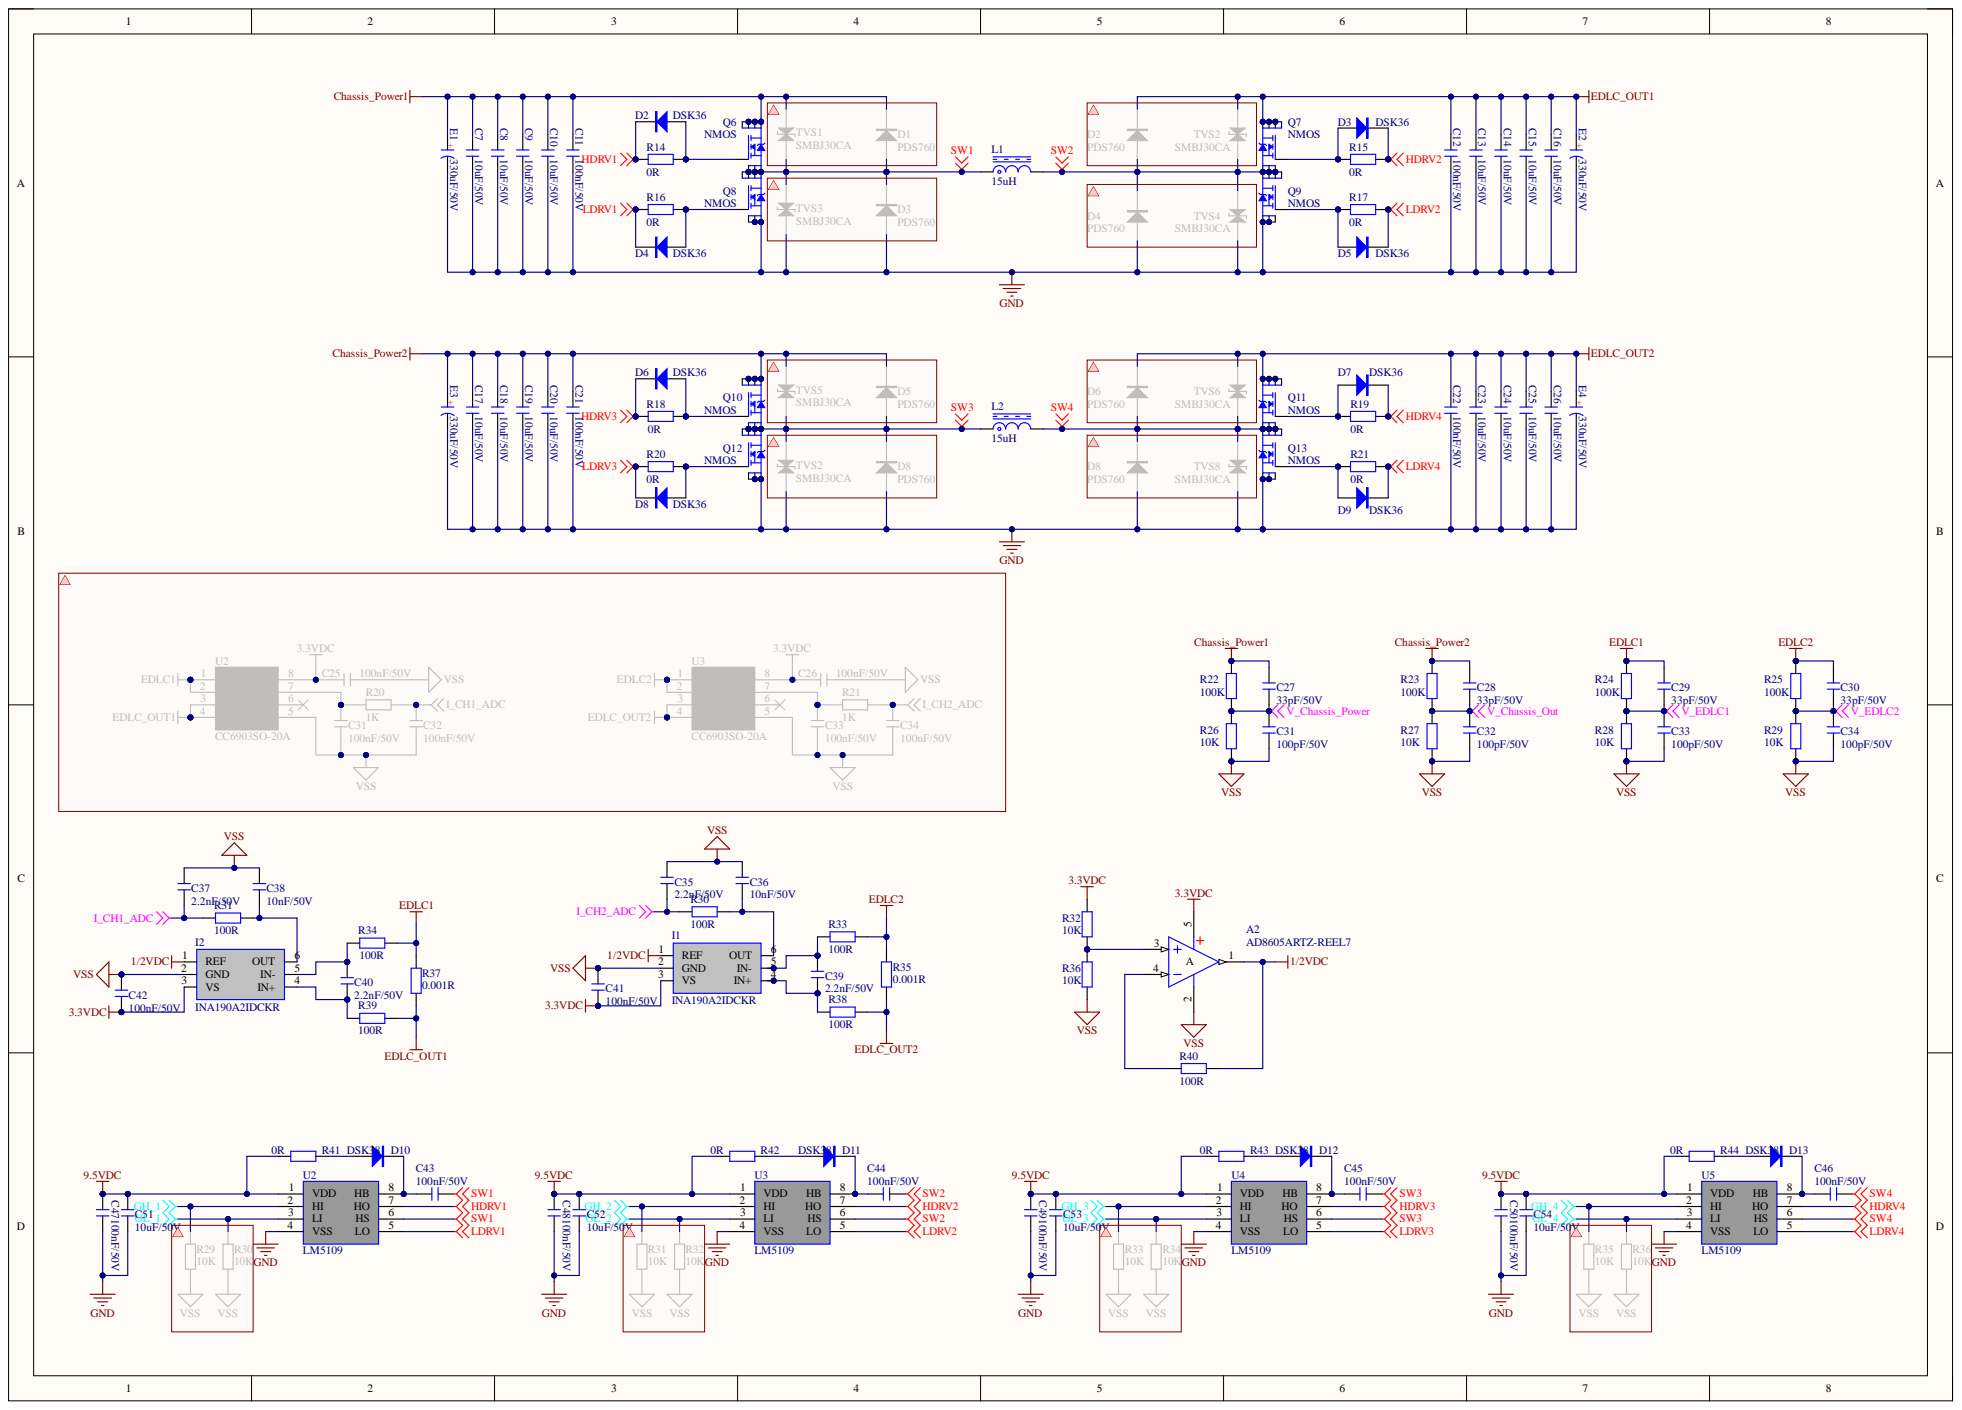
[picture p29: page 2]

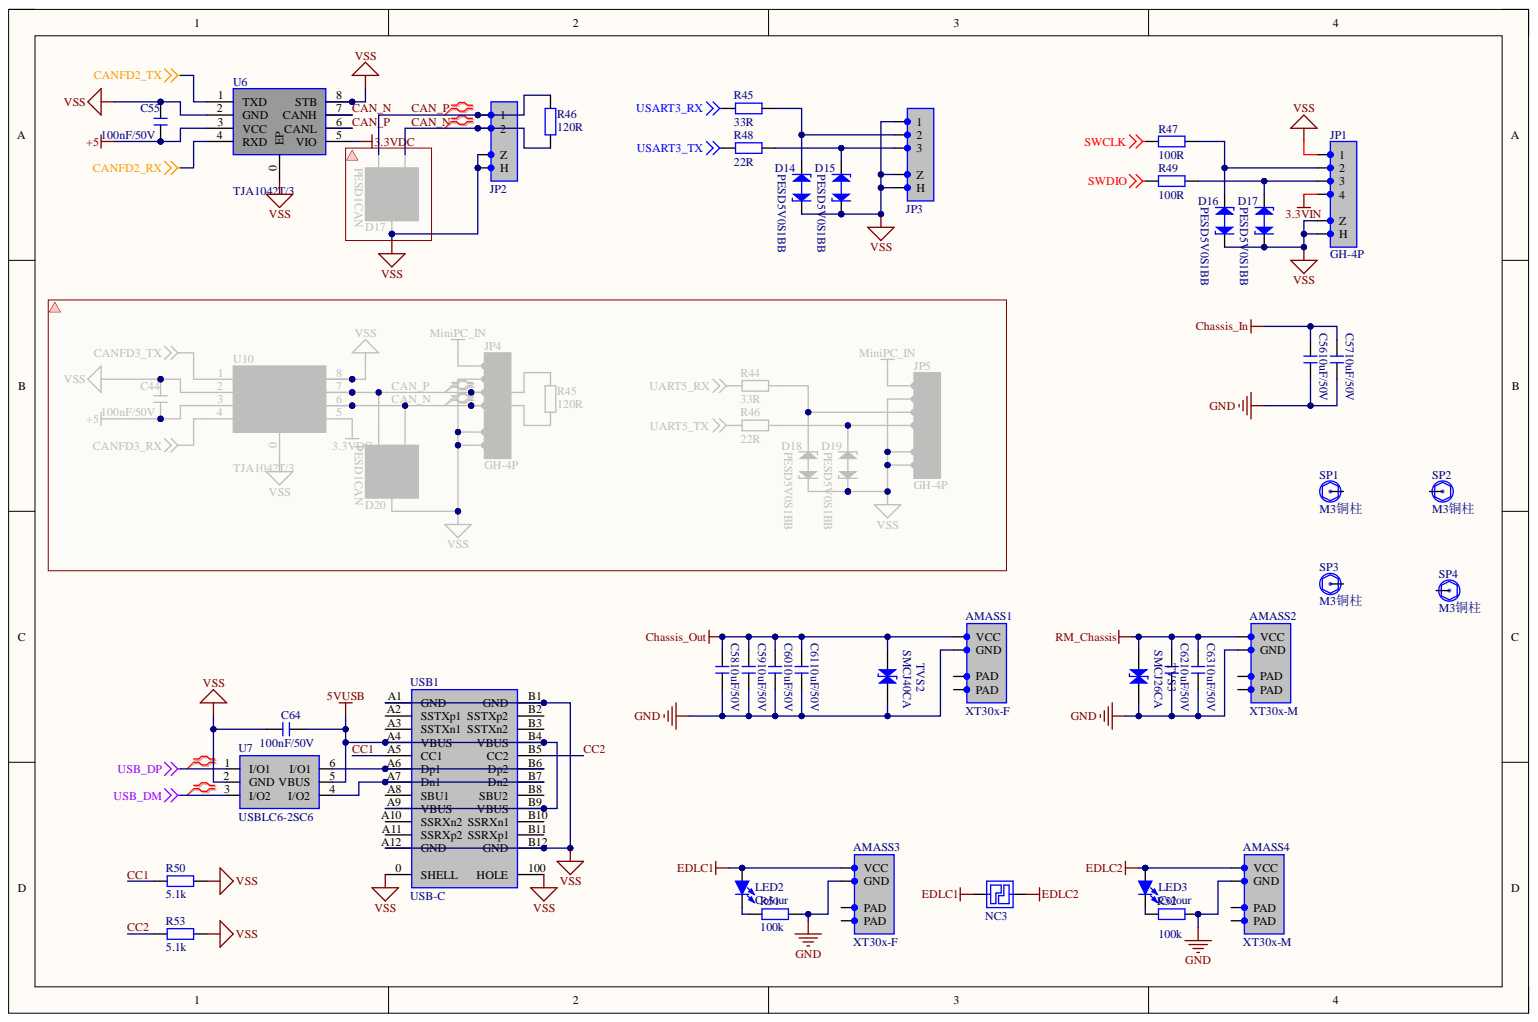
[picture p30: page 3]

TXD 1
GND 2
VCC 3 | CAN_N | 1

VCC 3 | | 4

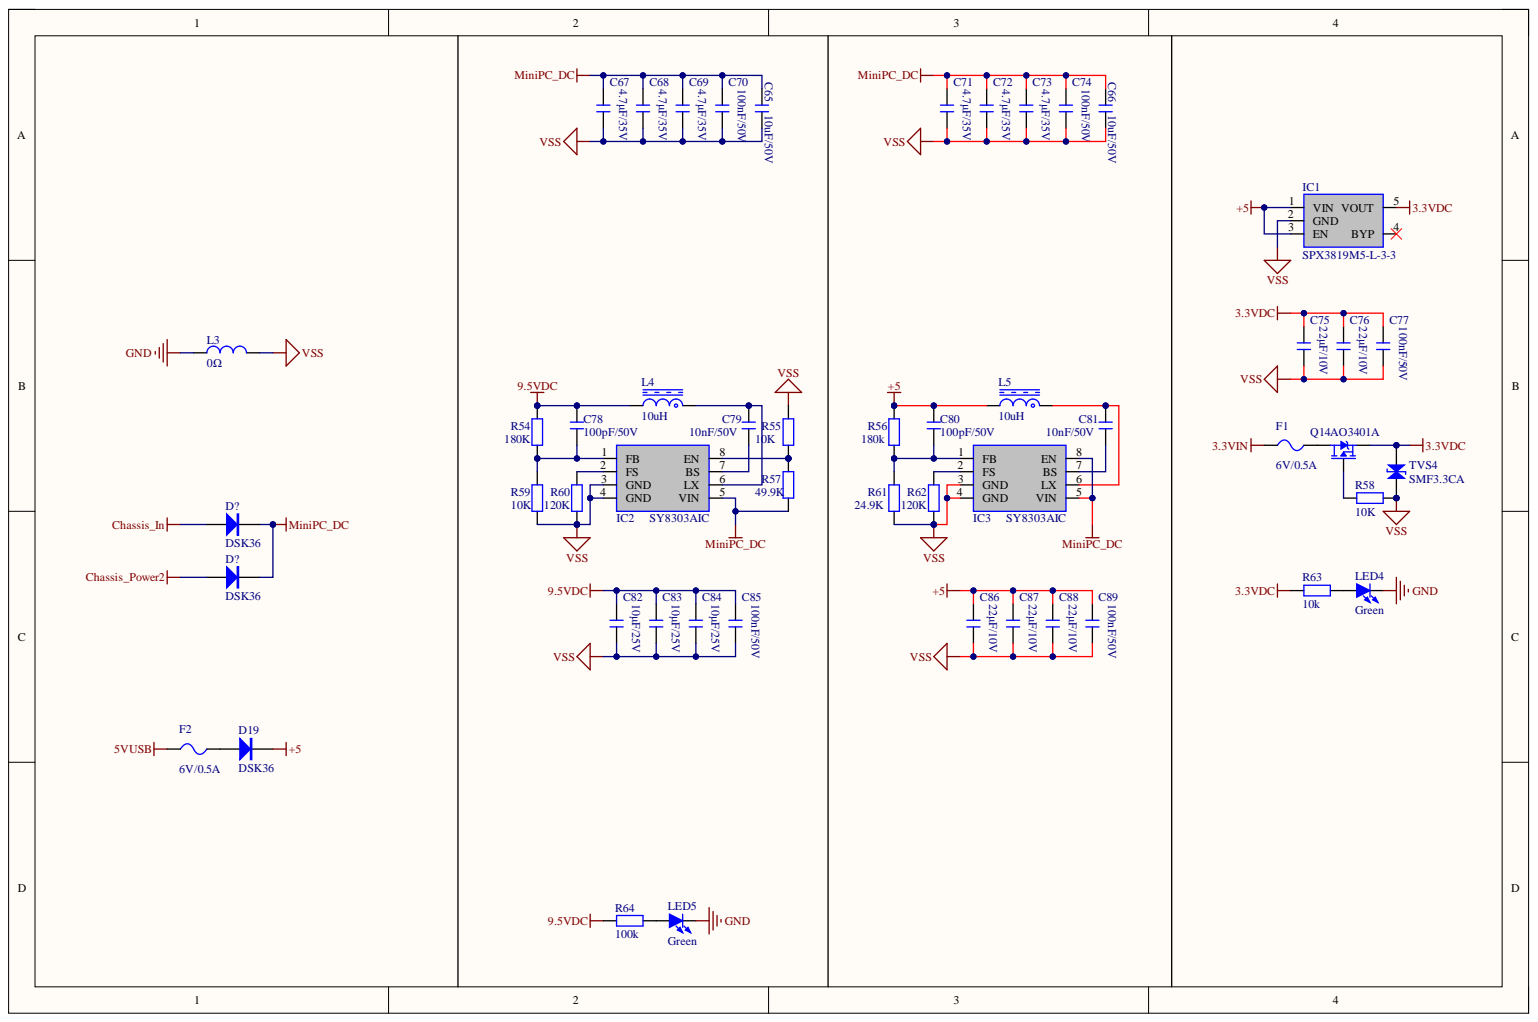
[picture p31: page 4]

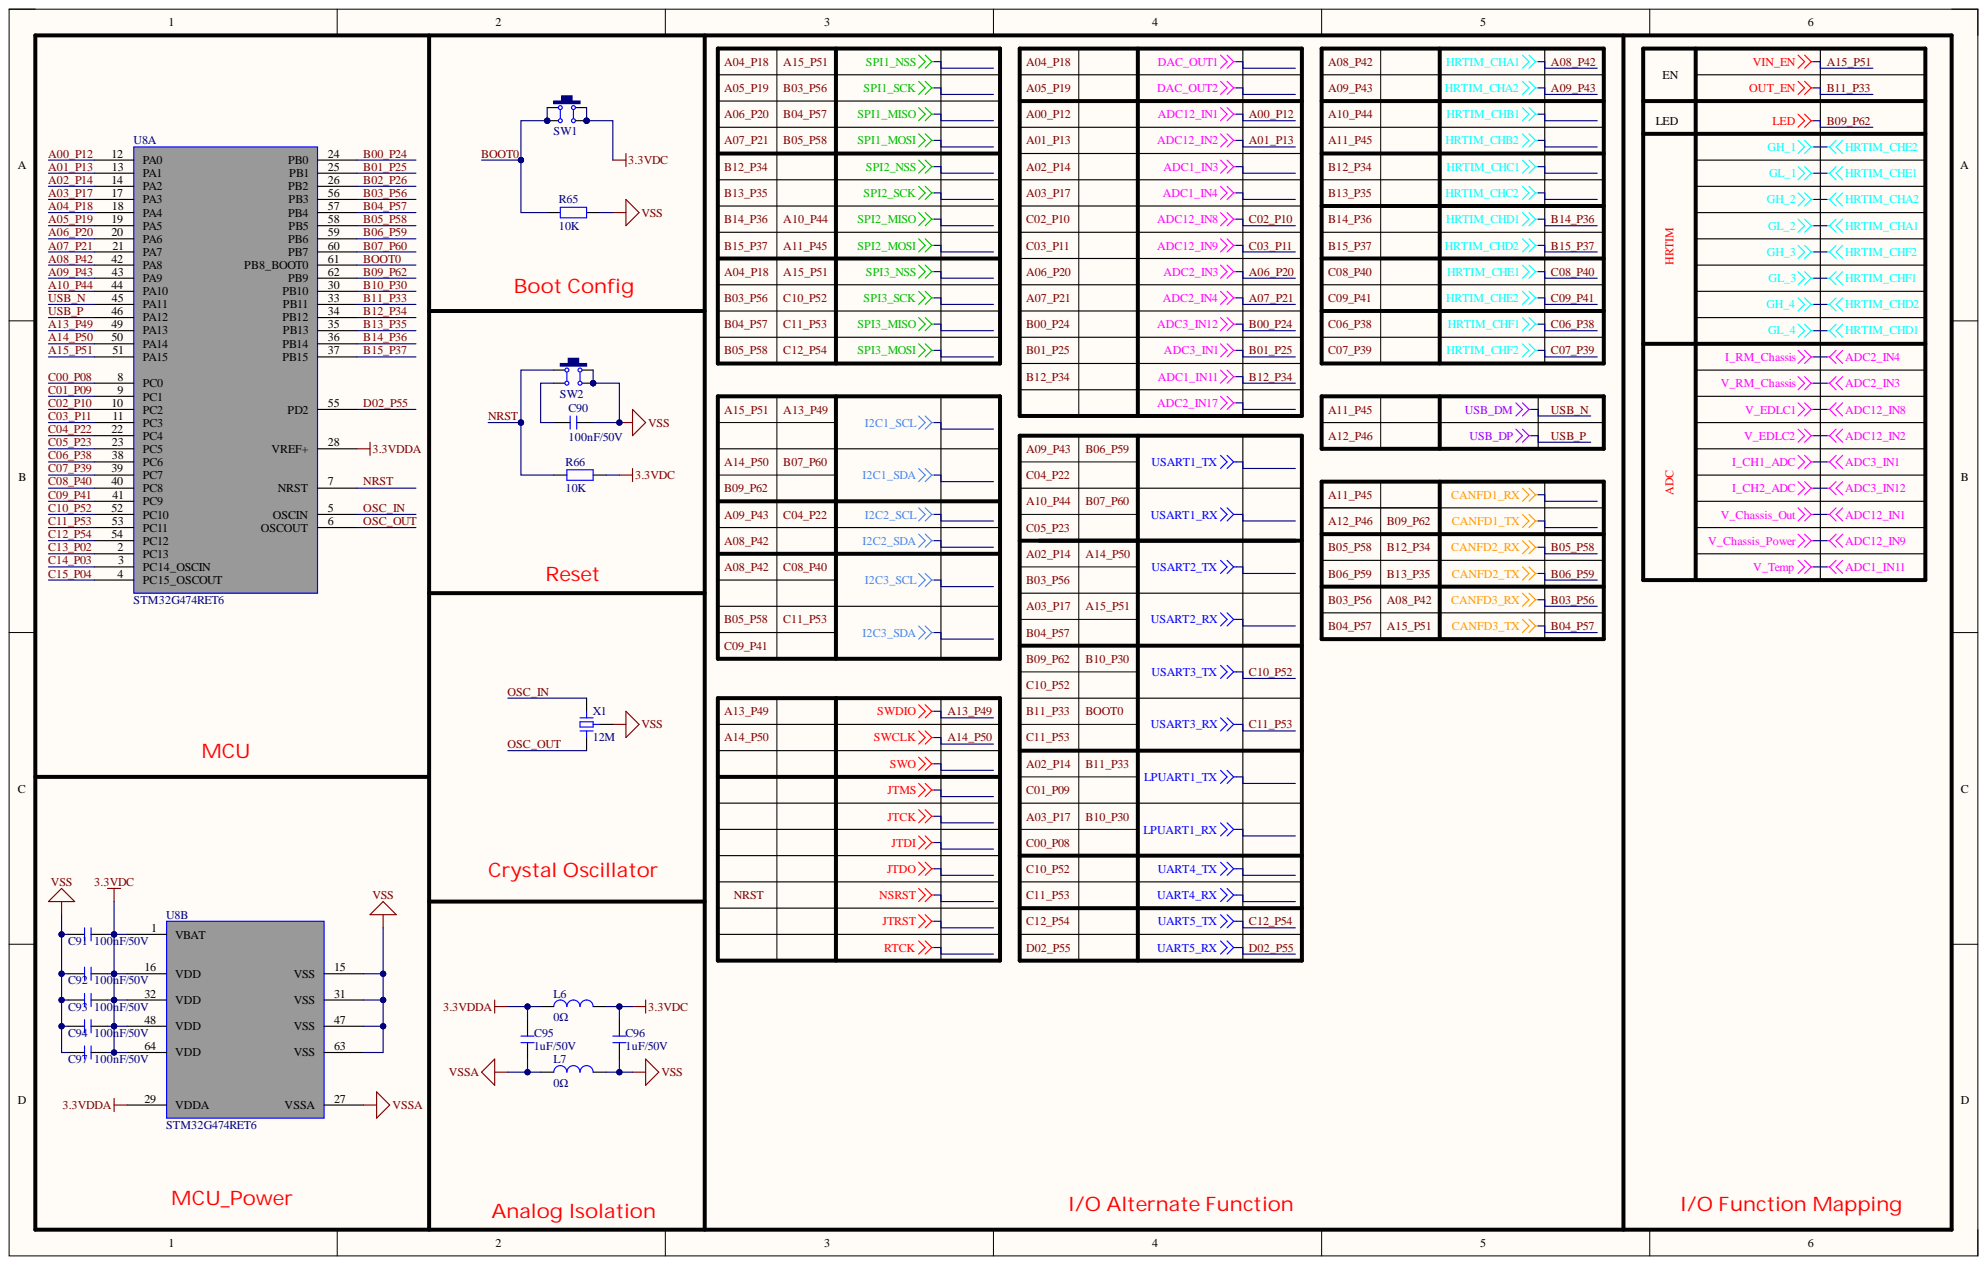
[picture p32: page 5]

GL_ 1 | HRTIM _ C HE 1

GH_ 2 | HRTIM _ C HA2

GH_ 3 | HRTIM _ C HF 2

GL_ 3 | HRTIM _ C HF 1

GH_4 | HRTIM _ C HD 2

GL_ 4 | HRTIM _ C HD 1

I_RM _Ch ass i s | ADC2 _ IN4

ADC2 _ IN 1 7

A0 9 _P4 3 | B0 6 _P 5 9 | USART1 _TX

A1 0 _P4 4 | B0 7 _P 6 0 | USART1 _RX

A1 2 _P4 6 | B0 9 _P 6 2 | CANFD1 _TX

B0 5 _P 5 8 | B1 2 _P 3 4 | CANFD2 _RX | B0 5 _P 5 8

A0 2 _P 1 4 | A1 4 _P 5 0 | USART2 _TX

B0 6 _P 5 9 | B1 3 _P 3 5 | CANFD2 _TX | B0 6 _P 5 9

B0 3 _P 5 6 | A0 8 _P4 2 | CANFD3 _RX | B0 3 _P 5 6

B0 4 _P 5 7 | A1 5 _P 5 1 | CANFD3 _TX | B0 4 _P 5 7

B0 9 _P 6 2 | B1 0 _P 3 0 | USART3 _TX | C1 0 _P 5 2

Comment | Description | Designator | Footprint | LibRef | Quantity
INA194AIDBVT | 电流感应放大器 80V | A1 | SOT23-5 | INA194AIDBVT | 1
AD8605ARTZ-REEL7 | 高精度低噪声CMOS 轨对轨输入/输出运 算放大器 | A2 | SOT23-5N | AD8605ARTZ-REEL7 | 1
XT30x-F | Amass防打火电源接 口，XT30系列 | AMASS1, AMASS3 | XT30U-F | XT30 | 2
XT30x-M | Amass防打火电源接 口，XT30系列 | AMASS2, AMASS4 | XT30U-M | XT30 | 2
100pF/50V | 无极性贴片电容 | C1, C31, C32, C33, C34, C78, C80 | C 0603_L | C | 7
100nF/50V | 无极性贴片电容 | C2, C6, C11, C12, C21, C22, C41, C42, C43, C44, C45, C46, C47, C48, C49, C50, C55, C64, C70, C74, C77, C85, C89, C90, C91, C92, C93, C94, C97 | C 0603_L | C | 29
10nF/50V | 无极性贴片电容 | C3, C36, C38, C79, C81 | C 0603_L | C | 5
2.2nF/50V | 无极性贴片电容 | C4, C5, C35, C37, C39, C40 | C 0603_L | C | 6
10uF/50V | 无极性贴片电容 | C7, C8, C9, C10, C13, C14, C15, C16, C17, C18, C19, C20, C23, C24, C25, C26, C51, C52, C53, C54, C56, C57, C58, C59, C60, C61, C62, C63, C65 | C 1206_L | C | 29
33pF/50V | 无极性贴片电容 | C27, C28, C29, C30 | C 0603_L | C | 4
10uF/50V | 无极性贴片电容 | C66 | C 0805_M | C | 1
4.7μF/35V | 无极性贴片电容 | C67, C68, C69, C71, C72, C73 | C 0603_L | C | 6
22μF/10V | 无极性贴片电容 | C75, C76, C86, C87, C88 | C 0603_L | C | 5
10μF/25V | 无极性贴片电容 | C82, C83, C84 | C 0603_L | C | 3
1uF/50V | 无极性贴片电容 | C95, C96 | C 0603_L | C | 2
PDS760 | 肖特基二极管 | D1 | SMPC | SS76 | 1
DSK36 | 高速开关二极管 | D2, D3, D4, D5, D6, D7, D8, D9 | SOD-323 | 1N4148 | 8
DSK38 | 肖特基二极管 | D10, D11, D12, D13 | SOD-123F | SS34 | 4
PESD5V0S1BB | 双向静电放电二极管 | D14, D15, D16, D17 | SOD-523 | ESD | 4
DSK36 | 肖特基二极管 | D19, D? | SOD-123F | SS34 | 3
BZT52C13S | 稳压二极管 | DZ1 | SOD-323 | CVD | 1
12V | 稳压二极管 | DZ2 | SOD-323 | CVD | 1
330uF/50V | 直插固态电容 | E1, E2, E3, E4 | CS 5.0*10*13 - R | C-CS | 4
6V/0.5A | 贴片保险丝 | F1, F2 | FU 0603 | FU | 2
INA190A2IDCKR | 电流感应放大器 40V | I1, I2 | SC-70-6 | INA190A2IDCKR | 2
SPX3819M5-L-3-3 | LDO线性稳压芯片 | IC1 | SOT23-5L | SPX3819 | 1
SY8303AIC | DC降压芯片 | IC2, IC3 | SOT23-8L | SY8303 | 2
GH-4P | 4P接插件 | JP1 | GH 1.25-LS-4P | Header 4 | 1
HDR-1X2 | 2P接插件 | JP2 | GH 1.25-LS-2P | Header 2 | 1
HDR-1X3 | 3P接插件 | JP3 | GH 1.25-LS-3P | Header 3 | 1
15uH | 一体成型电感 | L1, L2 | CKST2020-1717 | L-HP | 2
0Ω | 小功率贴片电感 | L3, L6, L7 | L 0603 | L | 3
10uH | 一体成型电感 | L4, L5 | CKST0502 | L-HP | 2
WS2812 | 全彩可控LED | LED1 | LED 3528-RGB | WS2812 | 1
Colour | 贴片LED | LED2, LED3 | LED 0603R | LED-SMD | 2
Green | 贴片LED | LED4, LED5 | LED 0603Y | LED-SMD | 2
NODE | 大电流节点 | NC1 | NODE-2 | NODE | 1
NODE | 大电流节点 | NC2, NC3 | NODE-3 | NODE | 2
NMOS | DFN封装N沟道场效 应管 | Q1, Q2, Q6, Q7, Q8, Q9, Q10, Q11, Q12, Q13 | DFN5*6-8L | NMOS_DFN | 10
NMOS | 贴片信号N沟道场效 应管 | Q3 | SOT23-3L | NMOS_SS | 1
PMOS | DFN封装P沟道场效 应管 | Q4, Q5 | DFN5*6-8L | PMOS_DFN | 2
AO3401A | 贴片信号P沟道场效 应管 | Q14 | SOT23-3L | PMOS_SS | 1
10k | 贴片电阻, NTC热敏 电阻 | R1, R3, R6, R10, R12, R55, R58, R63, R65, R66 | R 0603_L | R | 10
20k | 贴片电阻 | R2 | R 0603_L | R | 1
10R | 贴片电阻 | R4 | R 0603_L | R | 1
100K | 贴片电阻 | R5, R51, R52, R64 | R 0603_L | R | 4
1K | 贴片电阻 | R7 | R 0603_L | R | 1
100R | 贴片电阻 | R8, R9, R13, R30, R31, R33, R34, R38, R39, R40, R47, R49 | R 0603_L | R | 12
0.007R | 贴片电阻 | R11 | R 2512_M | R | 1
0R | 贴片电阻 | R14, R15, R16, R17, R18, R19, R20, R21, R41, R42, R43, R44 | R 0603_L | R | 12
100K | 精密贴片电阻 | R22, R23, R24, R25 | R 0603-HP_L | R-Precision | 4
10K | 精密贴片电阻 | R26, R27, R28, R29, R32, R36, R59 | R 0603-HP_L | R-Precision | 7
0.001R | 贴片电阻 | R35, R37 | R 2512_M | R | 2
33R | 贴片电阻 | R45 | R 0603_L | R | 1
120R | 贴片电阻 | R46 | R 0603_L | R | 1
22R | 贴片电阻 | R48 | R 0603_L | R | 1
5.1k | 贴片电阻 | R50, R53 | R 0603_L | R | 2
180K | 精密贴片电阻 | R54, R56 | R 0603-HP_L | R-Precision | 2
49.9K | 贴片电阻 | R57 | R 0603_L | R | 1
120K | 贴片电阻 | R60, R62 | R 0603_L | R | 2
24.9K | 精密贴片电阻 | R61 | R 0603-HP_L | R-Precision | 1
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

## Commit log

2024-09-06 Rename 屏幕截图 2024-07-03 203623-1721064569068-1.png to 模式示意.png
2024-09-06 更新图片
2024-09-06 更新PDF
2024-09-23 添加测试报告
2024-10-26 上传上位机
